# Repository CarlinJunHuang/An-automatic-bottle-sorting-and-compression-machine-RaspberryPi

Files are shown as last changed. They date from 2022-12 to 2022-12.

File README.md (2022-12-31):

# SDM242_Group5
2022 Fall SDM242 @Prof. Xiaoping Hong
# Background
This is the Github page of the fifth group in SDM242, Fall semester 2022.

The code in this home page covers the use of infrared sensors, inductive proximity switches, programmable LED light strips, electronic pulser handwheels, Raspberry PI stepper motors, 42 stepper motors, and 86 stepper motors.

These are the components and solutions we used/tried to use in the big project "Visual Beverage Bottle Sorting Compressor" in the semester.

See folder "Final_Program" for the whole final program.

# Details
If you want to replicate the functionality of the prototype we've done, you may need to use some of the following (recommended) components:

1. AC 220V to DC 24V/5V 150W power supply;
2. Raspberry PI;
3. 86 stepper motor with torque of at least 4Nm;
4. DMA860H drive;
5. Any 42 stepper motor;
6. TB6600 drive;
7. Infrared sensor;
8. Inductive proximity switch;
9. And... Maybe a computer is needed.

PS: The sensors mentioned in 7 and 8 can be purchased by yourself or made by referring to the samples in the "PCB" folder.

In addition, you may need some mechanical mechanism that can complete the given motion. Some of the main mechanisms I use are: screw lifting platform, slider platform and so on.

# References
In order to accomplish the goal of this final project, I looked up a lot of information on the Internet. Thanks all the kind ppl on the network for selfless dedication of their knowledge!

Followings are some of the most important references that have inspired me the most. I hope it also works for you!

[1]  Bilibili, https://www.bilibili.com/video/BV1gK411N73H/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.

[2]"Python GPIO.add_event_callback方法代码示例 - 纯净天空,"   Vimsky, https://vimsky.com/examples/detail/python-ex-LMK-GPIO-add_event_callback-method.html.

[3]"Python GPIO.add_event_detect方法代码示例 - 纯净天空,"   Vimsky, https://vimsky.com/examples/detail/python-method-RPi.GPIO.add_event_detect.html.

[4]"用户对问题“同时按两个按钮，GPIO.add_event_detect”的回答 - 问答 - 腾讯云开发者社区-腾讯云,"   Cloud, https://cloud.tencent.com/developer/ask/sof/334439/answer/567314.

[5]"[树莓派] 使用pigpio库(3) 如何发送指定数量的脉冲信号_The Daylight的博客-CSDN博客_pigpio,"   Blog, https://blog.csdn.net/weixin_52157994/article/details/124054827

[6]"树莓派使用Python检测连续脉冲 树莓派学习笔记,"   Readke, http://www.readke.com/c/01014010O2022.html.

[7]"一起玩转树莓派（16）——旋转编码传感器_51CTO博客_树莓派气压传感器,"   Blog, https://blog.51cto.com/u_11643026/4291087.

[8]"15“万里”树莓派小车——光电编码器学习（正反转的判断） - 创新实验室 - 电子工程世界-论坛,"   Bbs, http://bbs.eeworld.com.cn/thread-1188014-1-1.html.

[9]"树莓派使用Python检测连续脉冲 树莓派学习笔记,"   Readke, http://www.readke.com/c/01014010O2022.html.

[10]"Examples,"   Github, Dec. 5, 2021. https://github.com/wanli-car/Examples/blob/master/Python/Encoder_Count.py.

[11]D. Wilczak, "Control a Stepper Motor using Python and a Raspberry PI,"   Danielwilczak101, Apr. 25, 2021. https://danielwilczak101.medium.com/control-a-stepper-
motor-using-python-and-a-raspberry-pi-11f67d5a8d6d.

[12]"树莓派4B-使用 RPI.GPIO 模块的脉宽调制（PWM）功能_Hugo_yanghui的博客-CSDN博客_gpio pwm,"   Blog, https://blog.csdn.net/yhhdll0107/article/details/121627636.

[13]"运放的电压比较器电路_【ql君】qlexcel的博客-CSDN博客_运放比较电路,"   Blog, https://blog.csdn.net/qlexcel/article/details/79671016.

[14]"LM358组成的红外接收电路的工作原理,"   Wenwen, https://wenwen.sogou.com/z/q826293364.htm.

[15]"Proximity Sensors: Inductive and Capacitive Proximity Sensors with Arduino,"   Electroniclinic, https://www.electroniclinic.com/proximity-sensors-inductive-and-capacitive-proximity-sensors-with-arduino/.

[16]"科技小制作：制造简易金属探测器 – 科技小制作,"   Zhizuo, https://zhizuo.quwj.com/2020/12/09/1145.html.

[17]"如何使用TDA0161接近开关芯片制作一个金属探测器,"   Enroo, http://www.enroo.com/support/category1/dpjrmzs/41394529.html.

Today is 2022/12/31

And Wish you a Happy New Year!

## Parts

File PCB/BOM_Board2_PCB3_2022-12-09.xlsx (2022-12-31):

No. | Quantity | Comment | Designator | Footprint | Value | Manufacturer Part | Manufacturer | Supplier Part | Supplier
1 | 2 | 100nF | C1,C2 | C0603 | 100nF
2 | 1 | LM358S | IC1 | SOP-8_L4.9-W3.9-P1.27-LS6.0-BL |  | LM358S | Slkor(萨科微) | C408270 | LCSC
3 | 1 | 19-217/GHC-YR1S2/3T | LED1 | LED0603-R-RD |  | 19-217/GHC-YR1S2/3T | EVERLIGHT(亿光) | C72043 | LCSC
4 | 1 | 300 | R1 | R0603 | 300
5 | 1 | 30K | R2 | R0603 | 30K
6 | 1 | 50kΩ | R3 | RES-ADJ-TH_3362X | 50kΩ | 3362X-1-503LF | BOURNS | C123870 | LCSC
7 | 2 | 10K | R4,R5 | R0603 | 10K
8 | 1 | IR67-21C/TR8(GDB) | RI | LED-SMD_L3.1-W2.7-FD |  | IR67-21C/TR8(GDB) | EVERLIGHT(台湾亿光) | C131226 | LCSC
9 | 1 | PD15-22C/TR8(GPS) | RR | LED-SMD_4P-L3.3-W2.8-P1.40 |  | PD15-22C/TR8(GPS) | EVERLIGHT(台湾亿光) | C131271 | LCSC
10 | 1 | 2.54-3P接线端子 | U1 | CONN-TH_2.54-3P |  | 2.54-3P接线端子 | BOOMELE(博穆精密) | C68305 | LCSC

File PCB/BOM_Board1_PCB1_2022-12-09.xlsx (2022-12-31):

No. | Quantity | Comment | Designator | Footprint | Value | Manufacturer Part | Manufacturer | Supplier Part | Supplier
1 | 2 | 470pF | C1,C2 | C0603 | 470pF
2 | 1 | 300uH | L1 | L0603 | 300uH
3 | 1 | 2N2222A | Q1 | TO-92-3_L4.8-W3.7-P2.54-R |  | 2N2222A | BLUE ROCKET(蓝箭) | C358533 | LCSC
4 | 1 | 100kΩ | R1 | RES-ADJ-TH_3P-L9.6-W4.8-P2.50-R | 100kΩ | CT-94EX104 | NIDEC(尼得科) | C2921734 | LCSC
5 | 1 | 120 | R2 | R0603 | 120
6 | 1 | 500 | R3 | R0603 | 500
7 | 1 | 10K | R4 | R0603 | 10K
8 | 1 |  | U1 | SOP-8_L5.8-W3.9-P1.27-LS6.01BL
9 | 1 | 2.54-3P接线端子 | U2 | CONN-TH_2.54-3P |  | 2.54-3P接线端子 | BOOMELE(博穆精密) | C68305 | LCSC

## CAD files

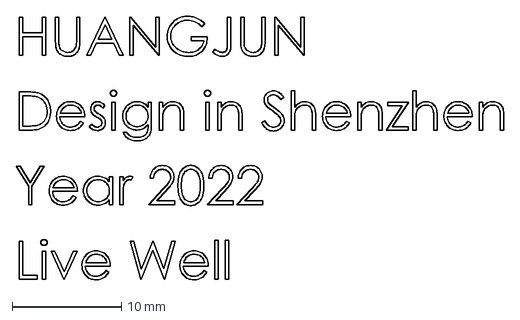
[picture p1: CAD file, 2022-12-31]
PCB/HJ.dxf
44.6 x 24.1 mm

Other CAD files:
PCB/HUANG.SLDPRT
PCB/Huang.dxf

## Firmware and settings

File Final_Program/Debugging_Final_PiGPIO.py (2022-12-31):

'''
    Driver for the motor (stepper motor).
    @author: Jingkai Zhang
    @version: 1.2
        version 1.1: add stepper motor (sofware PWM)
        version 1.2: add stepper motor (hardware PWM)
    @since: 2022
    @update: 2022-4-6
        edit in 2022-3-29: Add new stepper motor driver, based on pigpio, which is faster
        edit in 2022-4-3: Add more information if initialization is failed
        edit in 2022-4-6: fix some bugs
'''
import pigpio
import time, sys
import RPi.GPIO as GPIO
import os

GPIO.setwarnings(False)
GPIO.setmode(GPIO.BCM)

class stepper_motor42(object):
    num_of_steps_for_360 = 1600                 # this could be changed, please see the totorial of STR2/4
    resolution = num_of_steps_for_360 / 360     # resolution, how many steps would trigger 1 degree rotation
    DIR = 19                        # GPIO 18 for clockwise (physically connected to dir+ port in the driver)
    PUL = 13                        # GPIO 12 for counter clockwise (physically connected to step+ port in the driver)
    gear_ratio = 1                              # radius of the outer gear is 4 times than the radius of the inner gear
    cur_position = 0
    pwm_frequency = 3125                        # PWM frequency, the larger the faster rotation
    GPIO.setup(DIR, GPIO.OUT)
    '''
        TODO: decide how much frequency is suitable
        Here are some frequency that I recommend:
            5000 Hz, 6250 Hz, 10000 Hz, 12500Hz, 15625 Hz, 20000 Hz
        Better choose something that can be divided by 500000.
    '''
    inner_speed = 60 * pwm_frequency / num_of_steps_for_360
    outer_speed = inner_speed / gear_ratio
    delay_micro = int(500000 / pwm_frequency)
    CCW_wave = [pigpio.pulse(1 << PUL, 0, delay_micro), pigpio.pulse(0, 1 << PUL, delay_micro)]
    CW_wave = [pigpio.pulse(1 << DIR, 0, delay_micro), pigpio.pulse(0, 1 << DIR, delay_micro)]
    waveform_id = {}
    name = 'stepper_motor'

    def __init__(self):
        self.pi = pigpio.pi() 
        self.pi.wave_clear()
        self.pi.set_mode(self.PUL, pigpio.OUTPUT)
        self.pi.wave_add_generic(self.CCW_wave)
        self.waveform_id[self.PUL] = self.pi.wave_create()
        
    def __del__(self):
        self.pi = pigpio.pi()    
        self.pi.wave_tx_stop()  # stop waveform
        self.pi.wave_clear()
        self.pi.stop()

    def send_pulse(self, num_of_pulse, direction):
        '''
            If you want to know why, please visit the following link:
            https://abyz.me.uk/rpi/pigpio/python.html#wave_chain
        '''   
        x = int(num_of_pulse) & 255
        y = int(num_of_pulse) >> 8
        if direction == "left":
            GPIO.output(self.DIR, GPIO.LOW)
        elif direction == "right":
            GPIO.output(self.DIR, GPIO.HIGH)
        chain = [255, 0, self.waveform_id[self.PUL], 255, 1, x, y]  # send x + 256 * y times
        # chain = [255, 0, self.waveform_id[control_port], 255, 3]  # infinity loop, just for test
        self.pi.wave_chain(chain)
        while self.pi.wave_tx_busy():
            time.sleep(0.1)
        self.pi.wave_tx_stop() 

    def move(self, angle, direction):
        self.__init__()
        num_of_steps = self.resolution * angle * self.gear_ratio  # gear ratio is 3, so the outer speed is 1/4 of inner gear, need more pulse
        angle = -angle if direction == 'left' else angle           # decrease the angle if direction is CCW
        self.cur_position += angle
        print(self.cur_position)
        
        if self.cur_position > 10000 or self.cur_position < -10800:
            # self.log.error("rotation angle will exceeded 360 degree, wire might get twisted, current movement cancelled")
            # self.log.info("movement: <moved %d degree, direction:%s> has been cancelled" % (angle, direction))
            self.cur_position -= angle
            return False
        else:
            if direction == 'right':
                self.send_pulse(num_of_steps, "right")
            else:
                self.send_pulse(num_of_steps, "left")
            # self.log.info("moved %d degree, direction:%s, current position: %d" % (abs(angle), direction, self.cur_position))
            return True
        
    def get_motor_type(self):
        return self.name
    
class stepper_motor86(object):
    num_of_steps_for_360 = 1600                 # this could be changed, please see the totorial of STR2/4
    resolution = num_of_steps_for_360 / 360     # resolution, how many steps would trigger 1 degree rotation
    DIR = 18                        # GPIO 18 for clockwise (physically connected to dir+ port in the driver)
    PUL = 12                        # GPIO 12 for counter clockwise (physically connected to step+ port in the driver)
    gear_ratio = 3                              # radius of the outer gear is 4 times than the radius of the inner gear
    cur_position = 0
    pwm_frequency = 5000                        # PWM frequency, the larger the faster rotation
    GPIO.setup(DIR, GPIO.OUT)
    '''
        TODO: decide how much frequency is suitable
        Here are some frequency that I recommend:
            5000 Hz, 6250 Hz, 10000 Hz, 12500Hz, 15625 Hz, 20000 Hz
        Better choose something that can be divided by 500000.
    '''
    inner_speed = 60 * pwm_frequency / num_of_steps_for_360
    outer_speed = inner_speed / gear_ratio
    delay_micro = int(500000 / pwm_frequency)
    CCW_wave = [pigpio.pulse(1 << PUL, 0, delay_micro), pigpio.pulse(0, 1 << PUL, delay_micro)]
    CW_wave = [pigpio.pulse(1 << DIR, 0, delay_micro), pigpio.pulse(0, 1 << DIR, delay_micro)]
    waveform_id = {}
    name = 'stepper_motor'

    def __init__(self):
        self.pi = pigpio.pi() 
        self.pi.wave_clear()
        self.pi.set_mode(self.PUL, pigpio.OUTPUT)
        self.pi.wave_add_generic(self.CCW_wave)
        self.waveform_id[self.PUL] = self.pi.wave_create()
        
    def __del__(self):
        self.pi = pigpio.pi()    
        self.pi.wave_tx_stop()  # stop waveform
        self.pi.wave_clear()
        self.pi.stop()

    def send_pulse(self, num_of_pulse, direction):
        '''
            If you want to know why, please visit the following link:
            https://abyz.me.uk/rpi/pigpio/python.html#wave_chain
        '''   
        x = int(num_of_pulse) & 255
        y = int(num_of_pulse) >> 8
        if direction == "up":
            GPIO.output(self.DIR, GPIO.LOW)
        elif direction == "down":
            GPIO.output(self.DIR, GPIO.HIGH)
        chain = [255, 0, self.waveform_id[self.PUL], 255, 1, x, y]  # send x + 256 * y times
        # chain = [255, 0, self.waveform_id[control_port], 255, 3]  # infinity loop, just for test
        self.pi.wave_chain(chain)
        while self.pi.wave_tx_busy():
            time.sleep(0.1)
        self.pi.wave_tx_stop() 

    def move(self, angle, direction):
        self.__init__()
        num_of_steps = self.resolution * angle * self.gear_ratio  # gear ratio is 3, so the outer speed is 1/4 of inner gear, need more pulse
        angle = -angle if direction == 'up' else angle           # decrease the angle if direction is CCW
        self.cur_position += angle
        print(self.cur_position)
        
        if self.cur_position > 10800 or self.cur_position < -10800:
            # self.log.error("rotation angle will exceeded 360 degree, wire might get twisted, current movement cancelled")
            # self.log.info("movement: <moved %d degree, direction:%s> has been cancelled" % (angle, direction))
            self.cur_position -= angle
            return False
        else:
            if direction == 'down':
                self.send_pulse(num_of_steps, "down")
            else:
                self.send_pulse(num_of_steps, "up")
            # self.log.info("moved %d degree, direction:%s, current position: %d" % (abs(angle), direction, self.cur_position))
            return True
        
    def get_motor_type(self):
        return self.name
    
def setuppigpio():
    open_io="sudo pigpiod"
    os.system(open_io)
    time.sleep(1)
    pi = pigpio.pi()  # 初始化 pigpio库`

if __name__ == '__main__':
    #setuppigpio()
    sm86 = stepper_motor86()
    sm42 = stepper_motor42()
    #sm42.move(600, "left")
    #time.sleep(0.3)
    # sm86.move(2000, "down")
    #time.sleep(0.2)
    #sm86.move(1800, "down")
    # time.sleep(0.2)
    #sm86.move(500, "up")
    #time.sleep(0.01)
    #sm86.move(500, "up")
    #sm42.move(560, "right")
    time.sleep(0.2)
    #sm42.move(600, "left")
    sm86.move(3000, "up")
    time.sleep(0.15)
    sm86.move(3000, "up")
    time.sleep(0.15)
    #sm86.move(3000, "down")
    time.sleep(0.15)
    #sm86.move(3000, "up")

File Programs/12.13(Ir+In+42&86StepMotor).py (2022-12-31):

import RPi.GPIO as GPIO
import time

SM42freq = 19
SM42dirc = 26
SM86freq = 20
SM86dirc = 21
Inductive = 15
Infrared = 23
PulserA = 5
PulserB = 6
   
freq_StepMotor42 = 100
freq_StepMotor86 = 0
bottles = 0
mode = 0

def init():
    GPIO.setwarnings(False)
    GPIO.setmode(GPIO.BCM)
    GPIO.setup(Infrared, GPIO.IN)
    GPIO.setup(Inductive, GPIO.IN)
    GPIO.setup(SM42freq, GPIO.OUT)
    GPIO.setup(SM42dirc, GPIO.OUT)
    GPIO.setup(SM86freq, GPIO.OUT)
    GPIO.setup(SM86dirc, GPIO.OUT)

    GPIO.setup(PulserA, GPIO.IN, pull_up_down=GPIO.PUD_UP)
    GPIO.setup(PulserB, GPIO.IN, pull_up_down=GPIO.PUD_UP)
    pass

def detect():
    global bottles, mode
    while(bottles < 8):     # 控制最大容量，8只是测试值
        if GPIO.input(Infrared) == 0:    # 红外传感器，检测到瓶子投入
            time.sleep(1)
            bottles += 1
            print ("A bottle is coming in!")
            if GPIO.input(Inductive) == 0:
                mode = 1
            else:
                mode = 0
                
def sorting():
    global mode
    
def motor(freq, dirc, SMfreq, SMdirc):
    

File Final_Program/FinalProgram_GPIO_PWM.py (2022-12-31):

# HUANG JUN
import RPi.GPIO as GPIO
import time

IrPin  = 21
count = 0
countPC = 0
DIR86 = 18
PUL86 = 12
promixity_switchPin = 20

# 别问我这里为什么是2085不是1600，我也很纳闷，试了很久，发现这个频率才刚好转够一圈 > . <
speed86 = 2085


GPIO.setwarnings(False)
GPIO.setmode(GPIO.BCM)      # Numbers GPIOs by physical location
GPIO.setup([PUL86, DIR86], GPIO.OUT)
pwmPUL = GPIO.PWM(PUL86, 10*speed86) 

def setup():
    GPIO.setup(IrPin, GPIO.IN, pull_up_down=GPIO.PUD_UP)
    GPIO.setup(promixity_switchPin, GPIO.IN, pull_up_down=GPIO.PUD_UP)
    pwmPUL.start(0)


def cnt(ev=None):
	global count
	count += 1
	print ('Received infrared. cnt = ', count)
	GPIO.add_event_detect(promixity_switchPin, GPIO.FALLING, callback=promixityCallback)
	promixityDetect()
	

def rotate(time86, direction):
    GPIO.remove_event_detect(IrPin)
    """
    旋转操作，需要指定旋转角度和方向
    :param angle: 正整型数据，旋转角度
    :param direction: 字符串数据，旋转方向，取值为："ccw"或"cw".ccw:逆时针旋转，cw:顺时针旋转
    :return:None
    """
    if direction == "ccw":
        GPIO.output(DIR86, GPIO.LOW)
    elif direction == "cw":
        GPIO.output(DIR86, GPIO.HIGH)
    else:
        return
    pwmPUL.ChangeDutyCycle(50)
    time.sleep(time86)
    pwmPUL.ChangeDutyCycle(0)
    GPIO.add_event_detect(IrPin, GPIO.FALLING, callback=cnt)
    
def promixityDetect():
    
    GPIO.remove_event_detect(IrPin)
    GPIO.output(DIR86, GPIO.LOW)     # "ccw"
    pwmPUL.ChangeDutyCycle(50)
    time.sleep(5)
    pwmPUL.ChangeDutyCycle(0)
    GPIO.add_event_detect(IrPin, GPIO.FALLING, callback=cnt)
    GPIO.remove_event_detect(promixity_switchPin)
    
def compressPrepared():
    rotate(4, "cw")
    
def promixityCallback():
    GPIO.remove_event_detect(promixity_switchPin)
    global countPC
    countPC += 1
    print ('Received promixity. cnt = ', count)
    compressPrepared()
    
def loop():
	GPIO.add_event_detect(IrPin, GPIO.FALLING, callback=cnt) # wait for falling
	while True:
		pass   # Don't do anything

def destroy():
	GPIO.cleanup()                     # Release resource

if __name__ == '__main__':     # Program start from here
	setup()
	try:
		loop()
	except KeyboardInterrupt:  # When 'Ctrl+C' is pressed, the child program destroy() will be  executed.
		destroy()

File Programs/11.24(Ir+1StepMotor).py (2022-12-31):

import RPi.GPIO as GPIO
import time

# 红外+树莓派步进电机

IN1 = 19
IN2 = 26
IN3 = 20
IN4 = 21
IN5 = 15
IN6 = 23

    
delay = 0.002 #控制转速，增大则转速变慢  最快稳定转速大概为0.0017（这个速度想要转的话需要预热，不然转不起来）
steps = 128  #控制转动时长
bottles = 0
mode = 0

def init():
    GPIO.setwarnings(False)
    GPIO.setmode(GPIO.BCM)
    GPIO.setup(IN1, GPIO.OUT)
    GPIO.setup(IN2, GPIO.OUT)
    GPIO.setup(IN3, GPIO.OUT)
    GPIO.setup(IN4, GPIO.OUT)
    GPIO.setup(IN6, GPIO.IN)
    GPIO.setup(IN5, GPIO.IN, pull_up_down=GPIO.PUD_DOWN)
    pass

def detect():
    global bottles, mode
    while(bottles < 8):
        if GPIO.input(IN5) == 0:    
            print ("hahah")
            time.sleep(1)
        
        
        
        
def setStep(h1, h2, h3, h4):
    GPIO.output(IN1, h1)
    GPIO.output(IN2, h2)
    GPIO.output(IN3, h3)
    GPIO.output(IN4, h4)
    
def stop():
    setStep(0,0,0,0)
    
def step(direction):
    if direction == 1:
        for i in range(0, steps):
            setStep(1, 0, 0, 0)
            time.sleep(delay)
            setStep(0, 1, 0, 0)
            time.sleep(delay)
            setStep(0, 0, 1, 0)
            time.sleep(delay)
            setStep(0, 0, 0, 1)
            time.sleep(delay)
    else:
        for i in range(0, steps):
            setStep(0, 0, 0, 1)
            time.sleep(delay)
            setStep(0, 0, 1, 0)
            time.sleep(delay)
            setStep(0, 1, 0, 0)
            time.sleep(delay)
            setStep(1, 0, 0, 0)
            time.sleep(delay)
        
        
time.sleep(1)
init()
detect()
GPIO.cleanup()
